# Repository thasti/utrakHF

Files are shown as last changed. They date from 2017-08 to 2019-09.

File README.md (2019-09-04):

# utrakHF

A pico-balloon tracker implementing WSPR transmission on ham radio frequencies.

## Usage

For launch of this payload, a valid amateur radio callsign and permission for use on an airborne vehicle is required. To configure the software for flight, edit the defines for primary and secondary callsigns in tlm.h. The assignment of secondary callsigns is handled on KD2EAT's web site: http://hojoham.blogspot.com/2016/10/known-flight-ids.html

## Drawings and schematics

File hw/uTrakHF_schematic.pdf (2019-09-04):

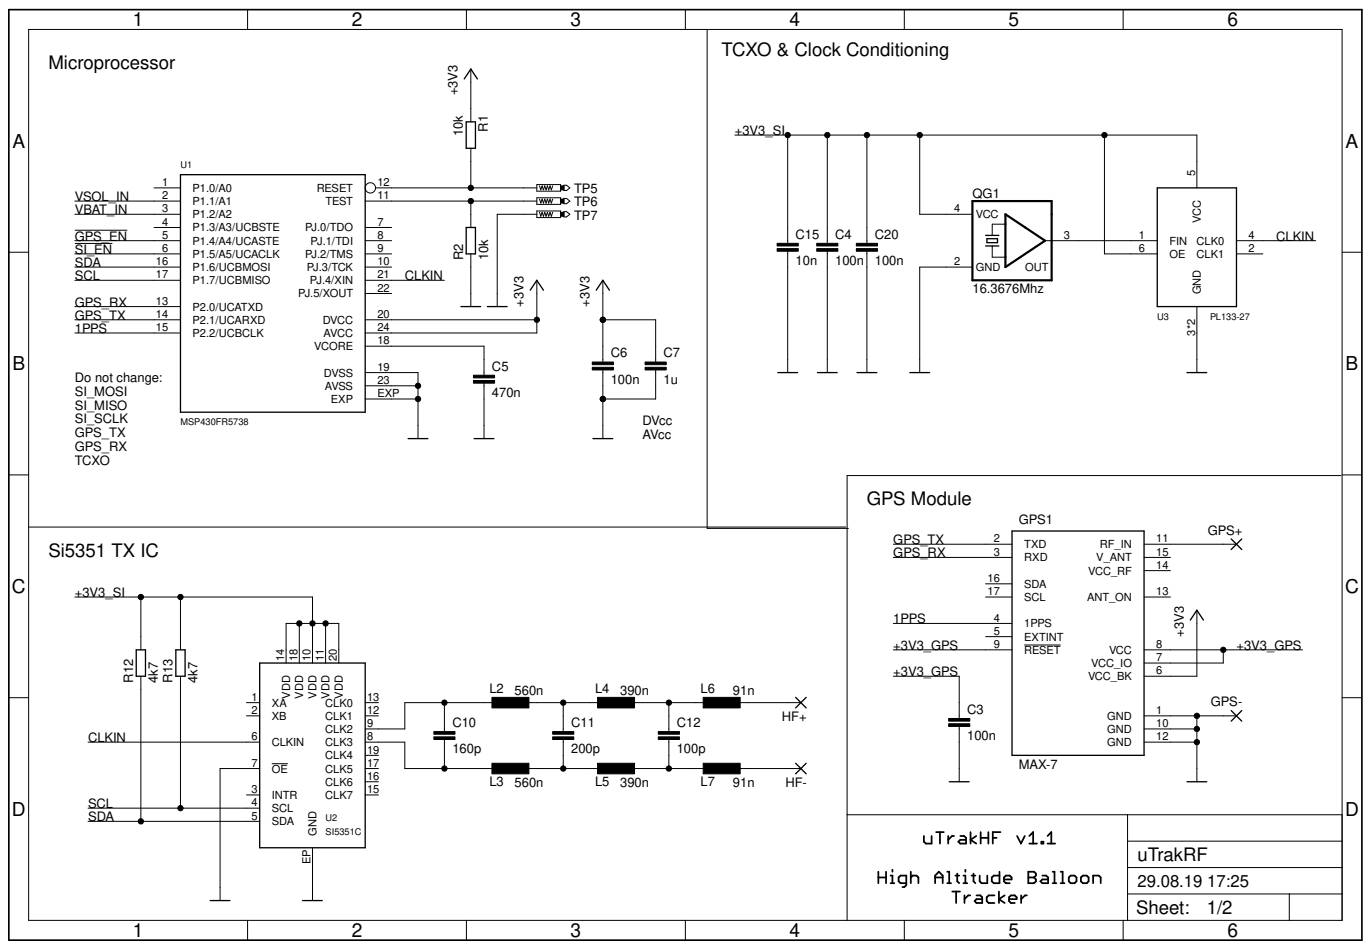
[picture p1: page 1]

TCXO & Clock Conditioning +3V3_SI

11 PJ.0/TDO 7 PJ.1/TDI 8 PJ.2/TMS 9 PJ.3/TCK

DVcc AVcc Do not change: SI_MOSI

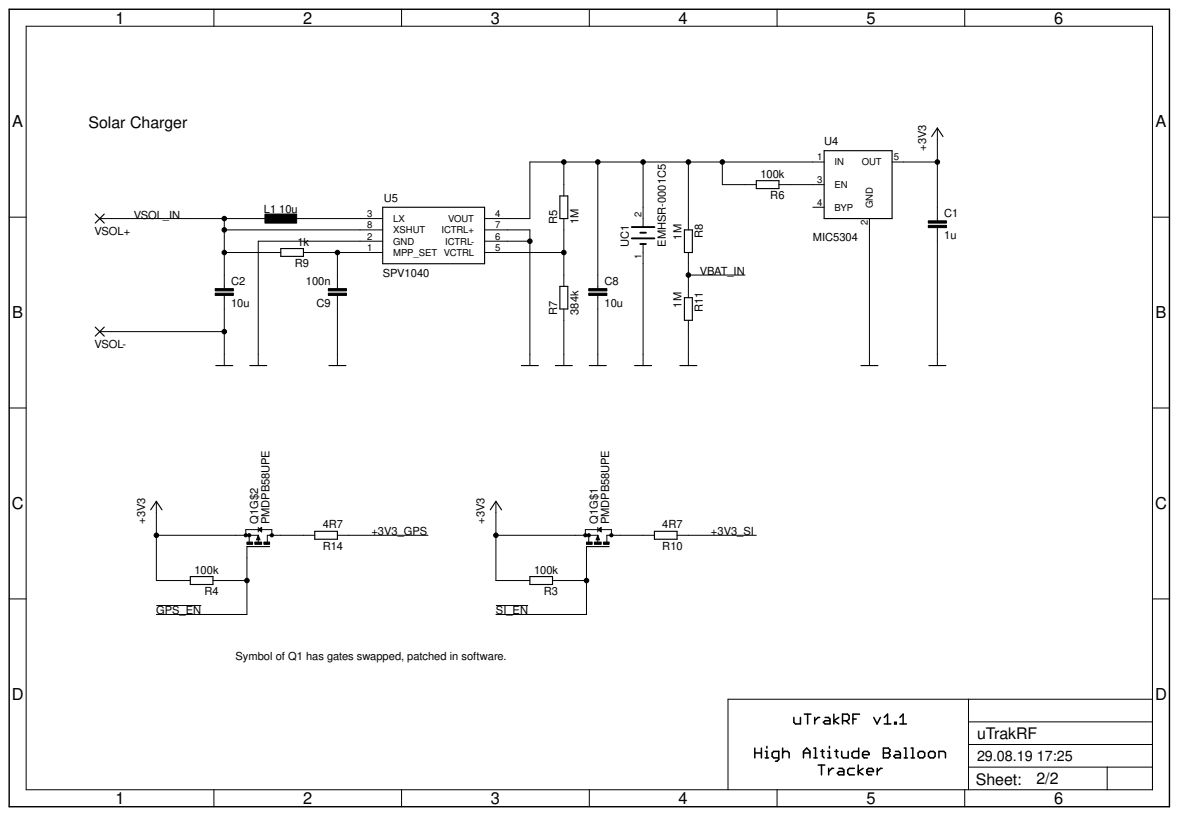
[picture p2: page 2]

Symbol of Q1 has gates swapped, patched in software.

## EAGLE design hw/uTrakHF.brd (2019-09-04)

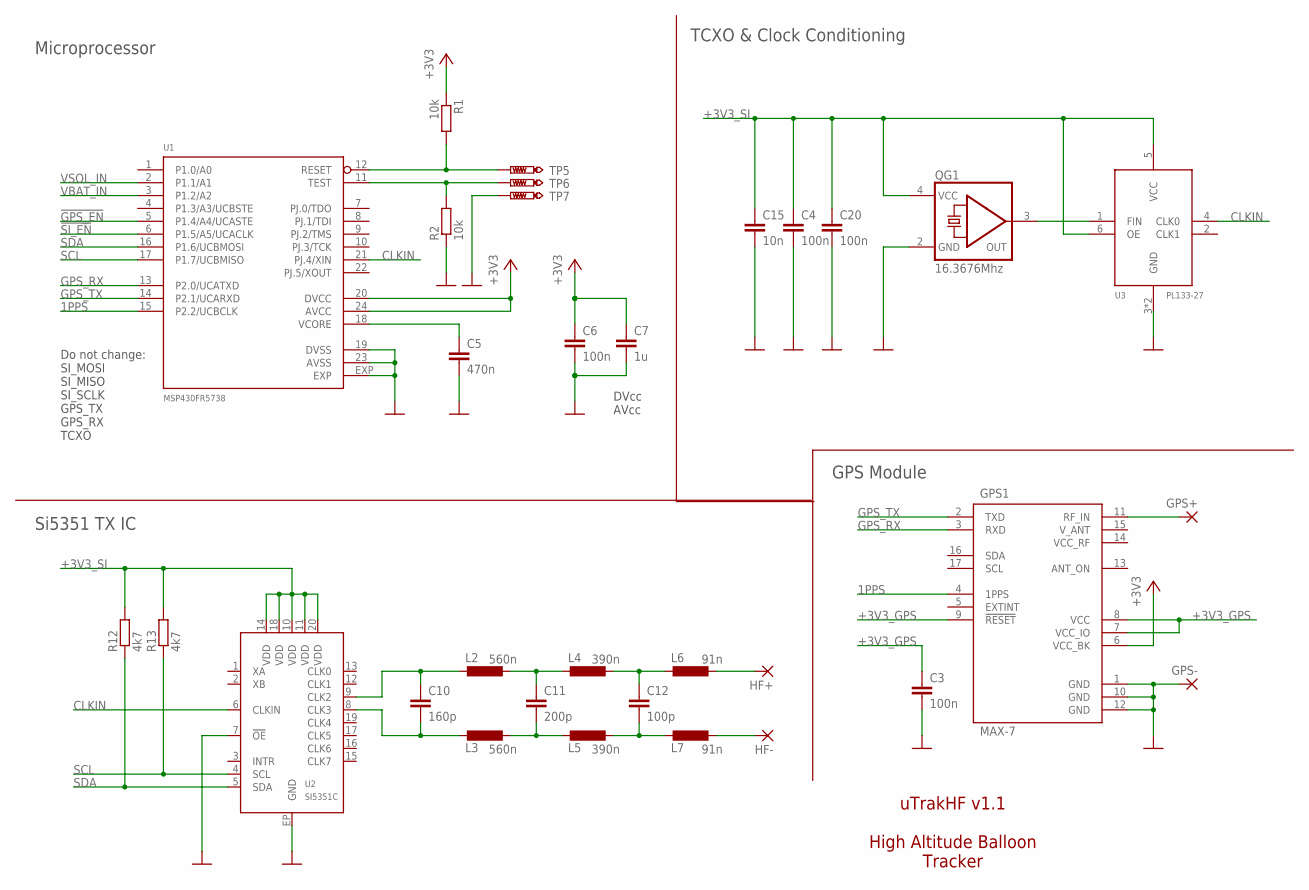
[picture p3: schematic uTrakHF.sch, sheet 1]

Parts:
C3, C4, C6, C20: 100n; C0402; PARTNO 81-GRM155R71C104KA88
C5: 470n; C0603; PARTNO 81-GCM188R71C474KA5D
C7: 1u; C0603; PARTNO 81-GRM39R105K10
C10: 160p; C0402; PARTNO 81-GRM1555C1H161JA01
C11: 200p; C0402; PARTNO 81-GRM1555C1H201JA1D
C12: 100p; C0402; PARTNO 81-GRM1555C1H101JA1D
C15: 10n; C0402; PARTNO 81-GRM155R71H103MA8D
GPS1: MAX-7; UBLOX-7
GPS+: SMD2; SMD1,27-2,54
GPS-: SMD2; SMD1,27-2,54
HF+: SMD2; SMD1,27-2,54
HF-: SMD2; SMD1,27-2,54
L2, L3: 560n; C0603; PARTNO 810-MLJ1608WR56JT000
L4, L5: 390n; C0603; PARTNO 810-MLJ1608WR39JT000
L6, L7: 91n; C0603; PARTNO 81-LQW18AN91NG00D
QG1: 16.3676Mhz; CTS406
R1, R2: 10k; R0402; PARTNO 603-RC0402FR-0710KL
R12, R13: 4k7; R0402; PARTNO 603-RC0402FR-074K7L
TP5, TP6, TP7: PTR1TP10SQ; TP10SQ
U1: MSP430FR5738; QFN24-4X4; PARTNO 595-SP430FR5738IRGER
U2: SI5351C; QFN20-4X4; PARTNO 634-SI5351C-B-GM
U3: PL133-27; DFN6-2X3; PARTNO 998-PL133-27GC-R

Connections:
1PPS: GPS1.4 (1PPS), U1.15 (P2.2/UCBCLK)
!GPS_EN: U1.5 (P1.4/A4/UCASTE); also elsewhere on the board
!SI_EN: U1.6 (P1.5/A5/UCACLK); also elsewhere on the board
+3V3: C6.1, C7.1, GPS1.6 (VCC_BK), R1.1, U1.20 (DVCC), U1.24 (AVCC); also elsewhere on the board
+3V3_GPS: C3.1, GPS1.7 (VCC_IO), GPS1.8 (VCC), GPS1.9 (!RESET); also elsewhere on the board
+3V3_SI: C4.1, C15.1, C20.1, QG1.4 (VCC), R12.2, R13.2, U2.10 (VDD), U2.11 (VDD), U2.14 (VDD), U2.18 (VDD), U2.20 (VDD), U3.5 (VCC), U3.6 (OE); also elsewhere on the board
C33: C10.1, L2.1, U2.9 (CLK2)
CLKIN: U1.21 (PJ.4/XIN), U2.6 (CLKIN), U3.4 (CLK0)
GND: C3.2, C4.2, C5.2, C6.2, C7.2, C15.2, C20.2, GPS1.1 (GND), GPS1.10 (GND), GPS1.12 (GND), GPS-.1, QG1.2 (GND), R2.1, TP7.TP, U1.19 (DVSS), U1.23 (AVSS), U1.EXP, U2.7 (!OE), U2.EP (GND), U3.3 (GND), U3.EXP (GND); also elsewhere on the board
GPS+: GPS1.11 (RF_IN), GPS+.1
GPS_RX: GPS1.3 (RXD), U1.13 (P2.0/UCATXD)
GPS_TX: GPS1.2 (TXD), U1.14 (P2.1/UCARXD)
HF+: HF+.1, L6.2
HF-: HF-.1, L7.2
unnamed: C5.1, U1.18 (VCORE)
unnamed: C11.1, L2.2, L4.1
unnamed: C12.1, L4.2, L6.1
unnamed: C10.2, L3.1, U2.8 (CLK3)
unnamed: C11.2, L3.2, L5.1
unnamed: C12.2, L5.2, L7.1
RST: R1.2, TP5.TP, U1.12 (RESET)
SCL: R13.1, U1.17 (P1.7/UCBMISO), U2.4 (SCL)
SDA: R12.1, U1.16 (P1.6/UCBMOSI), U2.5 (SDA)
TCXO: QG1.3 (OUT), U3.1 (FIN)
TST: R2.2, TP6.TP, U1.11 (TEST)
VBAT_IN: U1.3 (P1.2/A2); also elsewhere on the board
VSOL_IN: U1.2 (P1.1/A1); also elsewhere on the board

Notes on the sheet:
GPS Module
Microprocessor
DVcc AVcc
Do not change: SI_MOSI SI_MISO SI_SCLK GPS_TX GPS_RX TCXO
Si5351 TX IC
TCXO & Clock Conditioning
uTrakHF v1.1 High Altitude Balloon Tracker

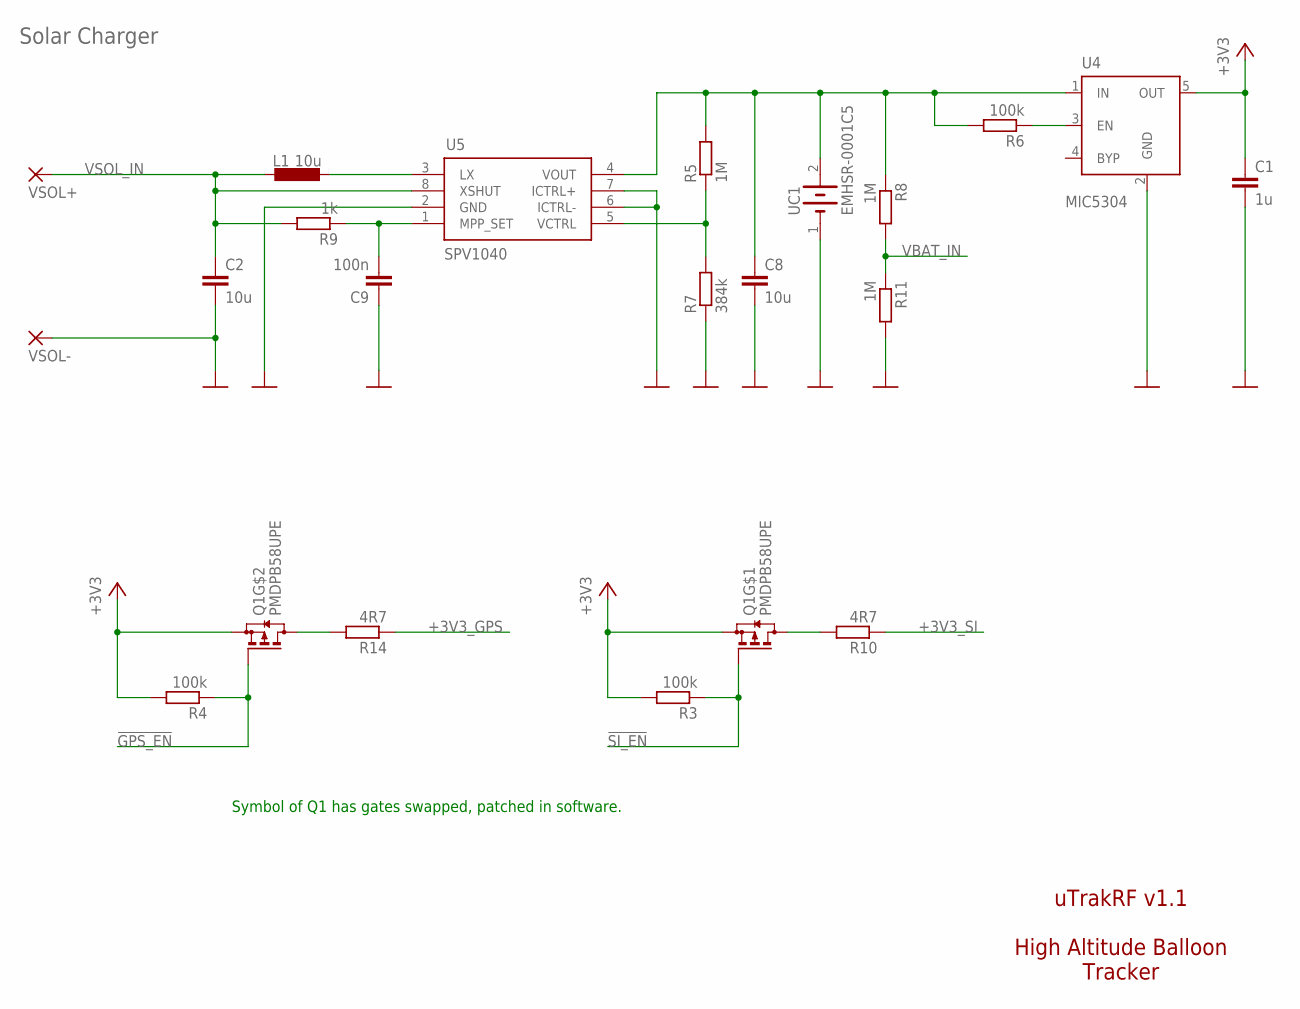
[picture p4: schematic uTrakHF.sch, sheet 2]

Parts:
C1: 1u; C0603
C2, C8: 10u; C0603
C9: 100n; C0402
L1: 10u; LPS4018; PARTNO 994-LPS4018-223MRB
Q1: PMDPB58UPE; SOT1118; PARTNO 771-PMDPB58UPE,115
R3, R4: 100k; R0402; PARTNO 603-RC0402FR-07100KL
R5: 1M; R0402
R6: 100k; R0402
R7: 384k; R0402
R8, R11: 1M; R0402; PARTNO 603-RC0402FR-071ML
R9: 1k; R0402
R10, R14: 4R7; R0402; PARTNO 603-RC0402FR-07100KL
U4: MIC5304; SOT23-5
U5: SPV1040; TSSOP8
UC1: EMHSR-0001C5; EMHSR-0001C5-005R0; PARTNO 581-SCMR22C155MRBA0
VSOL+: SMD2; SMD1,27-2,54
VSOL-: SMD2; SMD1,27-2,54

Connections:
!GPS_EN: Q1.5 (G), R4.1; also elsewhere on the board
!SI_EN: Q1.2 (G), R3.1; also elsewhere on the board
+3V3: C1.1, Q1.1 (S), Q1.4 (S), R3.2, R4.2, U4.5 (OUT); also elsewhere on the board
+3V3_GPS: R14.1; also elsewhere on the board
+3V3_SI: R10.1; also elsewhere on the board
GND: C1.2, C2.2, C8.2, C9.1, R7.1, R11.2, U4.2 (GND), U5.2 (GND), U5.6 (ICTRL-), U5.7 (ICTRL+), UC1.1 (-), VSOL-.1; also elsewhere on the board
unnamed: Q1.3 (D), Q1.8 (D), R10.2
unnamed: Q1.6 (D), Q1.7 (D), R14.2
unnamed: R6.1, U4.3 (EN)
unnamed: L1.1, U5.3 (LX)
unnamed: C9.2, R9.1, U5.1 (MPP_SET)
unnamed: R5.1, R7.2, U5.5 (VCTRL)
VBAT: C8.1, R5.2, R6.2, R8.1, U4.1 (IN), U5.4 (VOUT), UC1.2 (+)
VBAT_IN: R8.2, R11.1; also elsewhere on the board
VSOL_IN: C2.1, L1.2, R9.2, U5.8 (XSHUT), VSOL+.1; also elsewhere on the board

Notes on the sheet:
Solar Charger
uTrakRF v1.1 High Altitude Balloon Tracker
Symbol of Q1 has gates swapped, patched in software.

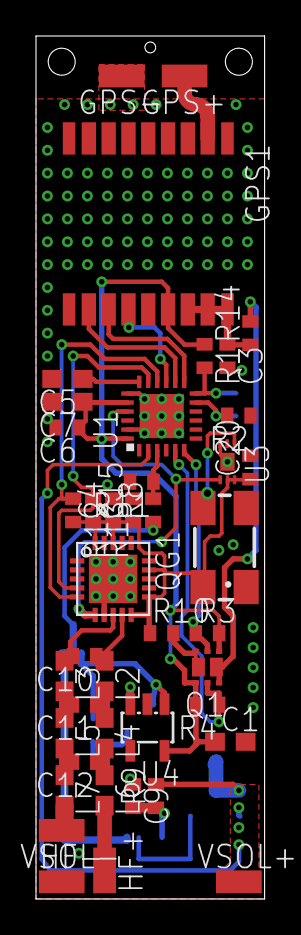
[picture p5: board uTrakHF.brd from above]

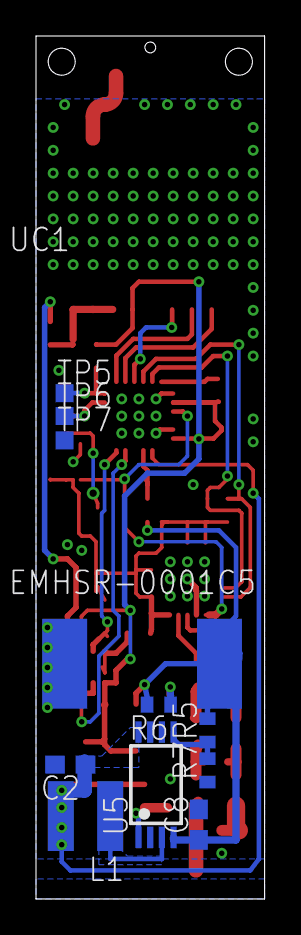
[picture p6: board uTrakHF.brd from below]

Board: 2 copper layers, 12.7 x 47.9 mm, 53 parts (11 on the bottom side), 34 nets.

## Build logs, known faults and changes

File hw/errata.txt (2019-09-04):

# uTrakHF PCB Errata
  * MOSFET pinout is wrong - impact: gates of GPS/Si5351 enable are swapped
    * currently fixed in software (pin swap)

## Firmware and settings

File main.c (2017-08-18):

#include <inttypes.h>
#include "adc.h"
#include "fix.h"
#include "gps.h"
#include "hw.h"
#include "main.h"
#include "si5351.h"
#include "tlm.h"
#include "wspr.h"

struct state;
struct wspr_message;
typedef void state_fn(struct state *);

struct state {
    state_fn *next;
    uint8_t wspr_symbol_count;
};

state_fn charge, get_gps_fix, transmit;

volatile uint16_t isr_flags = 0;
struct gps_fix fix;
struct wspr_message wspr_msg;

void charge(struct state *state) {
    uint16_t vbat, vsol;

    isr_flags |= ISR_FLAG_WAKE_CPU;
    hw_watchdog_feed();
    hw_enter_low_power_mode();
    isr_flags &= ~ISR_FLAG_WAKE_CPU;
    vbat = adc_get_voltage(CHANNEL_VBAT);
    vsol = adc_get_voltage(CHANNEL_VSOL);
    if (vbat > CHARGE_MIN_VBAT && vsol > CHARGE_MIN_VSOL) {
        /* battery charged, ready to proceed */
        state->next = get_gps_fix; 
        hw_gps_config(MODULE_ENABLE);
        gps_startup_delay();
        gps_disable_nmea_output();
        gps_set_airborne_model();
    }
}

void get_gps_fix(struct state *state) {
    uint16_t vbat, vsol;
    int16_t temp;
    
    while (!(isr_flags & ISR_FLAG_HEARTBEAT));
    isr_flags &= ~ISR_FLAG_HEARTBEAT;

    hw_watchdog_feed();
    vbat = adc_get_voltage(CHANNEL_VBAT);
    vsol = adc_get_voltage(CHANNEL_VSOL);
    temp = adc_get_temperature();
    gps_get_fix(&fix);
    if (vbat < FIX_MIN_VBAT || vsol < FIX_MIN_VSOL) {
        state->next = charge;
        hw_gps_config(MODULE_DISABLE);
    }
    if (fix.type == 3) {
        /* valid fix exists */
        if ((fix.min % 2) == 0 && (fix.sec == 0 || fix.sec == 1)) {
            /* start WSPR transmission */
            if (fix.min % 10 == 0) {
                tlm_encode_wspr_primary(fix.lat, fix.lon, temp, &wspr_msg);
            } else {
                tlm_encode_wspr_secondary(fix.lat, fix.lon, fix.alt, vsol, vbat, &wspr_msg);
            }
            wspr_encode(&wspr_msg);
            state->wspr_symbol_count = 0;
            state->next = transmit;
            hw_gps_config(MODULE_DISABLE);
            hw_rf_config(MODULE_ENABLE);
            si5351_startup_delay();
            si5351_init();
            isr_flags &= ~ISR_FLAG_WSPR_BAUD;
            hw_reset_wspr_baud_timer();
        }
    }
}

void transmit(struct state *state) {
    uint16_t vbat, vsol;

    while (!(isr_flags & ISR_FLAG_WSPR_BAUD));
    isr_flags &= ~ISR_FLAG_WSPR_BAUD;
    
    hw_watchdog_feed();
    if (state->wspr_symbol_count < WSPR_NUM_SYMBOLS) {
        si5351_set_channel(wspr_msg.tx_symbol_buffer[state->wspr_symbol_count++]);
    } else {
        state->next = charge;
        hw_rf_config(MODULE_DISABLE);
    }
    
    vbat = adc_get_voltage(CHANNEL_VBAT);
    vsol = adc_get_voltage(CHANNEL_VSOL);
    if (vbat < TX_MIN_VBAT || vsol < TX_MIN_VSOL) {
        state->next = charge;
        hw_rf_config(MODULE_DISABLE);
    }
}

int main(void) {
    struct state state = {charge, 0};
    hw_init();

    while(1) state.next(&state);
}

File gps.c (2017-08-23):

#include <msp430.h>
#include <inttypes.h>
#include "fix.h"
#include "hw.h"
#include "uart.h"

void gps_startup_delay(void);

/* 
 * gps_receive_ack
 *
 * waits for transmission of an ACK/NAK message from the GPS.
 *
 * returns 1 if ACK was received, 0 if NAK was received
 *
 */
uint8_t gps_receive_ack(uint8_t class_id, uint8_t msg_id) {
    int match_count = 0;
    int msg_ack = 0;
    char rx_byte;
    char ack[] = {0xB5, 0x62, 0x05, 0x01, 0x02, 0x00, 0x00, 0x00};
    char nak[] = {0xB5, 0x62, 0x05, 0x00, 0x02, 0x00, 0x00, 0x00};
    ack[6] = class_id;
    nak[6] = class_id;
    ack[7] = msg_id;
    nak[7] = msg_id;
    uart_flush_rx();

    /* runs until ACK/NAK packet is received, possibly add a timeout.
     * can crash if a message ACK is missed (watchdog resets */
    while(1) {
        rx_byte = uart_getc();
        if (rx_byte == ack[match_count] || rx_byte == nak[match_count]) {
            if (match_count == 3) {	/* test ACK/NAK byte */
                if (rx_byte == ack[match_count]) {
                    msg_ack = 1;
                } else {
                    msg_ack = 0;
                }
            }
            if (match_count == 7) { 
                return msg_ack;
            }
            match_count++;
        } else {
            match_count = 0;
        }
    }
}

/*
 * gps_receive_payload
 *
 * retrieves the payload of a packet with a given class and message-id with the retrieved length.
 * the caller has to ensure suitable buffer length!
 *
 * returns the length of the payload
 *
 */
uint16_t gps_receive_payload(uint8_t class_id, uint8_t msg_id, unsigned char *payload) {
    uint8_t rx_byte;
    enum {UBX_A, UBX_B, CLASSID, MSGID, LEN_A, LEN_B, PAYLOAD} state = UBX_A;
    uint16_t payload_cnt = 0;
    uint16_t payload_len = 0;

    uart_flush_rx();
    while(1) {
        rx_byte = uart_getc();
        switch (state) {
            case UBX_A:
                if (rx_byte == 0xB5)	state = UBX_B;
                else 			        state = UBX_A;
                break;
            case UBX_B:
                if      (rx_byte == 0x62)	state = CLASSID;
                else if (rx_byte == 0xB5)    state = UBX_B;
                else			state = UBX_A;
                break;
            case CLASSID:
                if (rx_byte == class_id)state = MSGID;
                else			state = UBX_A;
                break;
            case MSGID:
                if (rx_byte == msg_id)	state = LEN_A;
                else			state = UBX_A;
                break;
            case LEN_A:
                payload_len = rx_byte;
                state = LEN_B;
                break;
            case LEN_B:
                payload_len |= ((uint16_t)rx_byte << 8);
                state = PAYLOAD;
                break;
            case PAYLOAD:
                payload[payload_cnt] = rx_byte;
                payload_cnt++;
                if (payload_cnt == payload_len)
                    return payload_len;
                break;
            default:
                state = UBX_A;
        }
    }
}

/* 
 * gps_get_fix
 *
 * retrieves a GPS fix from the module. if validity flag is not set, date/time and position/altitude are 
 * assumed not to be reliable!
 *
 * argument is call by reference to avoid large stack allocations
 *
 */
void gps_get_fix(struct gps_fix *fix) {
    static uint8_t response[92];	/* PVT response length is 92 bytes */
    char pvt[] = {0xB5, 0x62, 0x01, 0x07, 0x00, 0x00, 0x08, 0x19};
    int32_t alt_tmp;

    /* request position */
    uart_puts(pvt, sizeof(pvt));
    gps_receive_payload(0x01, 0x07, response);

    fix->num_svs = response[23];
    fix->type = response[20];
    fix->year = response[4] + (response[5] << 8);
    fix->month = response[6];
    fix->day = response[7];
    fix->hour = response[8];
    fix->min = response[9];
    fix->sec = response[10];
    fix->lat = (int32_t) (
            (uint32_t)(response[28]) + ((uint32_t)(response[29]) << 8) + ((uint32_t)(response[30]) << 16) + ((uint32_t)(response[31]) << 24)
            );
    fix->lon = (int32_t) (
            (uint32_t)(response[24]) + ((uint32_t)(response[25]) << 8) + ((uint32_t)(response[26]) << 16) + ((uint32_t)(response[27]) << 24)
            );
    alt_tmp = (((int32_t) 
                ((uint32_t)(response[36]) + ((uint32_t)(response[37]) << 8) + ((uint32_t)(response[38]) << 16) + ((uint32_t)(response[39]) << 24))
               ) / 1000);
    if (alt_tmp <= 0) {
        fix->alt = 1;
    } else if (alt_tmp > 50000) {
        fix->alt = 50000;
    } else {
        fix->alt = (uint16_t) alt_tmp;
    }

}

/* 
 * gps_disable_nmea_output
 *
 * disables all NMEA messages to be output from the GPS.
 * even though the parser can cope with NMEA messages and ignores them, it 
 * may save power to disable them completely.
 *
 * returns if ACKed by GPS
 *
 */
uint8_t gps_disable_nmea_output(void) {
    char nonmea[] = {
        0xB5, 0x62, 0x06, 0x00, 20, 0x00,		/* UBX-CFG-PRT */
        0x01, 0x00, 0x00, 0x00, 			/* UART1, reserved, no TX ready */
        0xe0, 0x08, 0x00, 0x00,				/* UART mode (8N1) */
        0x80, 0x25, 0x00, 0x00,				/* UART baud rate (9600) */
        0x01, 0x00,					/* input protocols (uBx only) */
        0x01, 0x00,					/* output protocols (uBx only) */
        0x00, 0x00,					/* flags */
        0x00, 0x00,					/* reserved */
        0xaa, 0x79					/* checksum */
    };

    uart_puts(nonmea, sizeof(nonmea));
    //FIXME: sometimes, the ublox ACK is scrambled directly after power up...
    // however, it accepts the message and no harm is done.
    //return gps_receive_ack(0x06, 0x00);
    return 0;
}

/*
 * gps_set_gps_only
 *
 * tells the uBlox to only use the GPS satellites
 *
 * returns if ACKed by GPS
 *
 */
uint8_t gps_set_gps_only(void) {
    char gpsonly[] = {
        0xB5, 0x62, 0x06, 0x3E, 36, 0x00,		/* UBX-CFG-GNSS */
        0x00, 32, 32, 4,				/* use 32 channels, 4 configs following */
        0x00, 16, 32, 0, 0x01, 0x00, 0x00, 0x00,	/* GPS enable, all channels */
        0x03, 0, 0, 0, 0x00, 0x00, 0x00, 0x00,		/* BeiDou disable, 0 channels */
        0x05, 0, 0, 0, 0x00, 0x00, 0x00, 0x00,		/* QZSS disable, 0 channels */
        0x06, 0, 0, 0, 0x00, 0x00, 0x00, 0x00,		/* GLONASS disable, 0 channels */
        0xeb, 0x72					/* checksum */
    };

    uart_puts(gpsonly, sizeof(gpsonly));
    return gps_receive_ack(0x06, 0x3E);
}
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

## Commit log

2017-07-13 add low-level driver functionality
2017-07-13 implement Si5351 WSPR-optimized(tm) driver
2017-07-13 add GPS driver
2017-07-14 add battery / solar voltage limits for each operating state
2017-07-15 fix I2C write transfer
    [i2c.c]
2017-07-17 factor out delays into hw.c, review ADC settings
2017-07-18 add EAGLE design files
    [uTrakHF.brd, uTrakHF.sch]
2017-08-07 fix ADC measurement
2017-08-13 apply consistency fixes, fix solar/battery mixup
    [hw.c, hw.h, main.c]
2017-08-18 software fixes for I2C / Si5351
    [hw.c, i2c.c, main.c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]
2017-08-19 fix hw.c indentation, make ACLK = DCO/16
    [hw.c]
2017-08-22 fix Si5351 clock generation
    [si5351.c]
2017-08-22 use DCO/2 for UART
2017-08-22 don't wake up GPS, no power-save mode is used
2017-08-24 add new voltage limits
2017-08-24 fix missed ACLK dependencies for ADC
    [adc.c]
2018-04-18 fix init bug, change secondary call for 0x11
    [hw.c]
2018-05-02 add schematic PDF
2019-09-04 update hardware design documentation
    [uTrakHF.brd, uTrakHF.sch]
2019-09-22 revert back to first second transmission to decrease DT
    [main.c]
